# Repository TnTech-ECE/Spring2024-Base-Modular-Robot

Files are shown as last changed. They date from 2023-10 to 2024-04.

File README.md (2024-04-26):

# Modular IEEE Robot

## Executive Summary

Each year, Tennessee Technological University (Tech) participates in the Institute of Electrical and Electronics Engineers (IEEE) Southeastern Conference (SECON) hardware competition. The competition asks participants to create a robot that can perform various tasks, and competitors are scored based on their robot’s capability to complete tasks as quickly as possible. In past years, Tech has placed well, but the same problems have arisen each year that have inhibited wins: choppy navigation, shorted cables, and battery depletion are just a few of the many problems teams have repeatedly faced in previous competitions. The team sets out to fix the besetting problems that teams face each year not by competing in SECON, but rather by building a generalized platform that will optimize the basic robotic functionality for future teams. Sensing, movement, and centralized charging are the top priorities in the team’s design, all fitted together in a modular, adaptable framework that can be manipulated to fit most – if not all – IEEE hardware competition specifications. No longer will teams have to spend countless hours learning and designing movement systems or hoping everything works after rewiring a battery mid-competition. The design will take care of these basic competition necessities and leave the custom tailoring to the competition team.  

## Capabilities

The current version of the robot has the following capabilities:
1. Autonomous navigation
2. Modular components that can be easily adapted for different uses
3. Robust, centralized charging system
4. Functioning emergency stop button
5. Can travel inclines and declines up to 25 degrees
7. 360 degrees of movement
8. Knows location within a 2 inch tolerance
9. Sensors are are plug and play adpatable with the use of an I2C bus
10. Foundation layed for autonomous navgivaton with LiDAR and ROS2
11. User manual for teams to understand design considerations, common problems, and solutions

## Salient Outcomes

As projects progress, there are typically outcomes tht are more impressive than others. Here is a list of salient outcomes of this project:
1. Wireless charging proof of concept
2. Multiple navigation subsets for teams to choose between
3. Foundation for layed for ROS2 mapping for future uses
4. Plug and play adapatibility with sensors through I2C buses
5. Power board with ground isolation
6. GUI for teams to see their live data transmission 

## Project Demonstration & Images

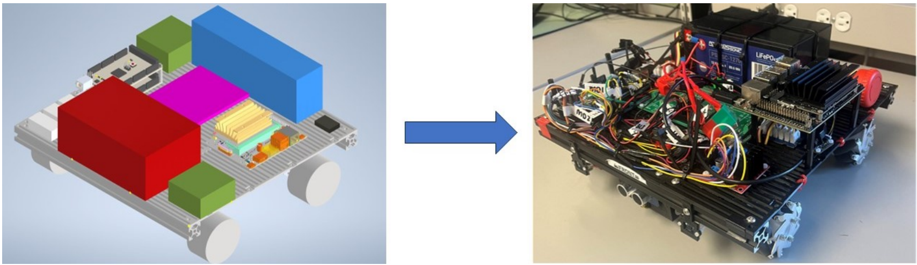
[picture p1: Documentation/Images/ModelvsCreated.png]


3D model of the robot vs the final product

[Watch the video](https://youtu.be/stM9KGa8I_E) of the robot autonomously navigating a line.

[Watch the video](https://youtu.be/3MeIy1WahUA) of the robot autonomously sweeping the board given its location.

[Watch the video](https://youtu.be/3MeIy1WahUA](https://www.youtube.com/watch?v=_iFhnvbLboQ)) of the robot detecting objects in front of it.

## About Us

### Team

**[Luke Chapman](https://www.linkedin.com/in/luke-chapman-/)** is an electrical engineering major at Tennessee Technological University with a minor in mathematics. He is interested in electromagnetics, telecommunications, and signal processing. Luke is responsible for the power management and distribution systems of the robot as well as the experimental wireless power charging system.

**[Reid Crews](https://www.linkedin.com/in/jackson-crews-381187257/)** is an electrical engineering major, mechatronics concentration at Tennessee Technological University with a minor in mathematics. Reid's interests are mechatronics and control systems. For the project, Reid is a contributor for the navigation sensing, primarily the location and object detection subsystems.

**[Isaac Hoese](https://www.linkedin.com/in/isaac-hoese-425748251)** is a senior electrical engineering student from Greeneville, Tn. He is interested in both power system analysis and embedded system design. In this project, Isaac will be a contributor for the navigation sensing, primarily the line following and orientation subsystems.

**[Isaac Jennings](www.linkedin.com/in/isaac-jennings-a04680209)** is a senior electrical engineering student with a minor in mathematics from Church Hill, TN. He takes interest in control systems, programming, and embedded systems, which is where he allocated his time by working on the master control systems on the project. He is responsible for the navigation and localization of the robot as it interfaces with the game board.  

**[Abigail Kennedy](https://www.linkedin.com/in/abigail-kennedy-tech/)** is an electrical engineering major at Tennessee Technological University with minors in mathematics and education. Abigail's primary interest is in controls and PLC design, and for this project, she worked on the motor control subsystem to ensure the robot can move quickly and smoothly.

**[Mabel Olson](https://www.linkedin.com/in/mabelolson/)** is an electrical engineering major at Tennessee Technological University with a minor in mathematics. She is intrested in power and control systems. In this project, Mabel is responsible for the chassis design, robot layout, organization, and any 3D designing of component attachment pieces. 

### Faculty Supervisor

The faculty supervisor for this project is [Dr. Nan Chen][def1]. She completed her electrical and control engineering Bachelor's degree from Nanjing University of Aeronautics and Astronautics. She also completed her Master's and Ph.D. in electrical engineering from the University of Waterloo. 

[def1]: https://www.linkedin.com/in/nan-chen-319aa185/

### Stakeholders

The primary customer for the project is [Professor Jesse Roberts](https://www.linkedin.com/in/jessetnroberts/) - the advisor for the IEEE SECON hardware teams. Future teams are impacted by this design but unable to be stakeholders, so he gives input on their behalf based on his years of experience with the competition.

### Recognitions

We would like to recognize and thank Professor Jesse Roberts, Dr. Nan Chen, and Dr. Charles Van Neste for their continuous input and guidance on the project.

## Repo Organization

### [Reports](/Reports)

The [Project Proposal](./Reports/Project%20Proposal/Project%20Proposal%20Revised.pdf) is the initial document for the project where the problem is defined and the goals for the project.

The [Conceptual Design](./Reports/Conceptual%20Design/Conceptual%20Design%20and%20Planning%20V2.pdf) gives a more detailed solution to the problem as well as subsystem breakdowns and a projected timeline and budget.

The [Experimentation](/Documentation/Experimental%20Analysis) gives the experimental results of the different subsystems and how constraints were met or not.

The [Poster](./Reports/Poster/Modular%20IEEE%20Robot%20Poster.pdf) is what the team presented at the 2024 capstone showcase.

The [Final Presentation](./Reports/Final%20Presentation/Final%20Presentation.pdf) is the presentation that the team gave to the IAB.

The [Lessons Learned](./Reports/LessonsLearnedAndAquiredSkills.md) gives team members' reflections on their progress, oversights, noteable incidents, and successes.

### [Documentation](/Documentation)
All documentation for the project is included in the above folder. Documentation includes all schematics, images, models, BOM, and designs used in the project.

The [Meeting Minutes](/Documentation/Meeting%20Minutes) folder contains the dated minutes from weekly meetings and allows a quick view into the progress of the team.

[Signoffs](/Documentation/Signoffs) are used to finalize designs for each subsystem. This includes schematics, design decisions, BOM, and analysis. 

### [Software](/Software)

 All software used and created is listed in the [Software](./Software) directory. For each subsystem, there are specific folders listed to find the necessary code.

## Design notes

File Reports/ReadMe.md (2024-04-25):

# Reports

The final version of the following are found here in Reports:

1. [Project Proposal](https://github.com/lchapman42/Control-Sensing-Wireless-Charging-Robot/blob/main/Reports/Project%20Proposal/Project%20Proposal%20Revised.pdf)
2. [Conceptual Design and Planning](https://github.com/lchapman42/Control-Sensing-Wireless-Charging-Robot/blob/main/Reports/Conceptual%20Design/Conceptual%20Design%20and%20Planning%20V2.pdf)
3. [Poster](https://github.com/lchapman42/Control-Sensing-Wireless-Charging-Robot/blob/main/Reports/Poster/Modular%20IEEE%20Robot%20Poster.pdf)
4. [Lessons Learned](https://github.com/lchapman42/Control-Sensing-Wireless-Charging-Robot/blob/main/Reports/LessonsLearnedAndAquiredSkills.md)
5. [Final Presentation](https://github.com/lchapman42/Control-Sensing-Wireless-Charging-Robot/blob/main/Reports/Final%20Presentation/Final%20Presentation.pdf)

## Examples

The following capstone projects were helpful in writing our reports:

[SECON 2022](https://github.com/TnTech-ECE/Spring2022-SECON2022)

[SECON 2023](https://github.com/TnTech-ECE/Spring2023-SECONRobot)

[Crawlspace Robot](https://github.com/TnTech-ECE/Fall-2023-2.0-Autonomous-Crawlspace-Inspection-Robot)

[Active Noise Control](https://github.com/CarsonDPope/Active-Noise-Control-With-Wall-Transmission-Detection)

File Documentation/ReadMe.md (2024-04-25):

# Documentation

Each of the folders have the team's designs, research, and useful images used for the project. It also contains the team's meeting notes and plans for the future of the project. A final BOM was determined after purchasing everything for this iteration.

## Signoffs

Signoffs are the detailed part of the design process which includes the schematics, bill of materials, specifications, and justifications. The signoffs have been approved by Dr. Nan Chen and were also advised by Dr. Jessee Roberts.

## Final set of prints (final design artifacts)



### 3D Models

Required format: 
3D models can be found [here](https://github.com/lchapman42/Control-Sensing-Wireless-Charging-Robot/tree/main/Documentation/3D%20Models), and they have been updated throughout the project.

### Wiring Schematics and PCB

All schematics and PCB designs can be found [here](https://github.com/lchapman42/Control-Sensing-Wireless-Charging-Robot/tree/main/Documentation/Electrical). 

## Final BOM

The final version of the BOM can be seen as a [pdf](https://github.com/lchapman42/Control-Sensing-Wireless-Charging-Robot/blob/main/Documentation/Final%20BOM.pdf) or in the original [exel file](https://github.com/lchapman42/Control-Sensing-Wireless-Charging-Robot/blob/main/Documentation/Final%20BOM.xlsx).

## Datasheet 

The [user manual](https://github.com/lchapman42/Control-Sensing-Wireless-Charging-Robot/tree/main/Reports) in the reports section can be used to see how each of the subsystems work in detail and connect.

## The project poster

The project poster that summarizes the final results of the project is [here](https://github.com/lchapman42/Control-Sensing-Wireless-Charging-Robot/tree/main/Reports/Poster).

## Detailed photos of the project

Detailed photos of the project can be found [here](https://github.com/lchapman42/Control-Sensing-Wireless-Charging-Robot/tree/main/Documentation/Images).

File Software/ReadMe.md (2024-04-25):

## Bluetooth Reveiver
This code is for an ESP32. The reciever microcontroller needs to be connected to a laptop. The GUI can be ran to read sensor data when the Nav_Full code is ran. The code recieves the signal sent by the transmitter.

## Bluetooth Transmitter
This code is for an ESP32. The transmitter micrconcontroller needs to be connected to the on-robot Arduino Mega 2560. The code creates ESP Now packets to be sent to the reciever.

## 2023_Board
This code is ran on the on-robot Arduino Mega 2560 for object detection and position sensing without a line present. (Not used with ROS)

## Line Following
This code is ran on the on-robot Arduino Mega 2560 for line following. The code uses PID control method to control navigation. (Not used with ROS)

## Nav_Full 
This code is ran on the on-robot Arduino Mega 2560. This code encapsulates all sensor readings and is used alongside the jetson nano. The code has no navigation capability as ROS completes those tasks.

*All Arduino Mega and ESP32 code is compiled with the Arduino IDE*

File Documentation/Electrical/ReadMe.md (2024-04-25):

This directory contains all of the electrical schematics and PCB files. The PCB directory contains files for the simulation, schematics, and design of the power distribution PCB. The Schematics directory contains the files for the Arduino schematic. The Testing directory contains data from testing the battery life and some notes taken while performing tests on the different power subsystems.

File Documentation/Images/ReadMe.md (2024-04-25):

This directory contains images used in each of the signoffs and experimental analysis, they are elaborated in their respective sections:
- [Signoffs](https://github.com/lchapman42/Control-Sensing-Wireless-Charging-Robot/tree/main/Documentation/Signoffs)
- [Experimental Anaylsis](https://github.com/lchapman42/Control-Sensing-Wireless-Charging-Robot/blob/main/Documentation/Experimental%20Analysis/Experimental%20Analysis.md)

There are also videos of different experiments and the robot movement in the experimental analysis section.

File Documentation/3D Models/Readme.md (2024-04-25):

The 3D models directory has the .stl files for the 3D printed components created for this project.

The .stl files can be viewed in GitHub and used with other 3D editing software. Please see the respective sign offs for more information on the components.

- [Attachments](https://github.com/lchapman42/Control-Sensing-Wireless-Charging-Robot/blob/main/Documentation/Signoffs/Attachment%20Signoff.md)
- [Chassis](https://github.com/lchapman42/Control-Sensing-Wireless-Charging-Robot/blob/main/Documentation/Signoffs/Chassis%20Frame%20Sign%20Off.md)
- [Layout & Organization](https://github.com/lchapman42/Control-Sensing-Wireless-Charging-Robot/blob/main/Documentation/Signoffs/Layout%20and%20Organization.md)

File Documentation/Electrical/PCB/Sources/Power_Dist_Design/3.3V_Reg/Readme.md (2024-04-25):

In this directory there are files for a SPICE simulation of the buck converter chip. The SPICE model of the buck converter was gotten from the manufacturer, Texas Instruments. To perform the simulation simply run the .asc file with LTSpice or another SPICE simulation software. There is only a simulation of the 3.3V layout, there was 5V layout originally but it was removed on accident some time ago. The only difference between the 3.3V and 5V simulations is a single resistor value, which can be easily determined in the datasheet. This is discussed more in the signoff for the power distribution system.

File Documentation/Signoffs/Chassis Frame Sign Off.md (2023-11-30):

# Chassis Frame Signoff

## Functionality 

The function of this subsystem is to be the structure of the robot. This will allow ll components to be connected together through a strong frame.

## Constraints

- C3: The robot shall be autonomous with customizable dimensions and the stock design only occupying up to one-half of the allowed cubic foot (1 ft x 1 ft x 6 in).
	- This constraint is applicable to the chassis frame because the frame will be the standward way for custom dimensions. Therefore, the material needs to allow for easy movement of sides, come in multiple sizes, and be able to be cut if possible. It is important to note that the stock design will be occupying 1 foot by 1 foot area. The height will be mainly effected by the motors, components, and their trays.

- C4: The robot shall contain modules that are plug and play adaptable for different IEEE competition requirements.
	- This constraint is applicable to the chassis frame subsystem because components need to have the ability to be added, removed, and or moved easily. The chassis frame will be what every component is attached to; therefore, the a material selected needs to allow for easy attachment method.

### Derived from Broader Impacts

- The frame will need to be able to withstand 20 pounds.
	- This stems from a typical weight standard of 25 pounds that had to be reduced due by the customer due to not being able to reach an incline and speed specifcation with a 25 pound load with avaliable motors.

## Buildable Schematics
The following schematics outline the dimensions for the extrusion itself and the layout for the chassis. The chassis frame layout was decided through many decisions. Trying to take up as much of the 1 foot by 1 foot area was the largest concern. 1 foot is 304.8 mm. Therefore, the 300 mm frame peices were used for the front and rear bars. The 250 mm bars are used for the side bars and nested inside the 300 mm bars. This will make the width to be 300 mm and the length to be 290 mm because the width of the bars is 20 mm. The side bars are nested inside due to the motors and wheels. They add width to the frame and therefore if the bars are nested they can be moved in or out to adhere to dimension requirements. The placement in the schematics allow for maximum occupency of the space. The middle bar is there to add more support and for better tray movement, but can be removed if decided that it is not needed in the tray subsystem. The middle rod does not have to be centralized as it is in the schematic. It can be moved based on what is needed for the tray sizes.  
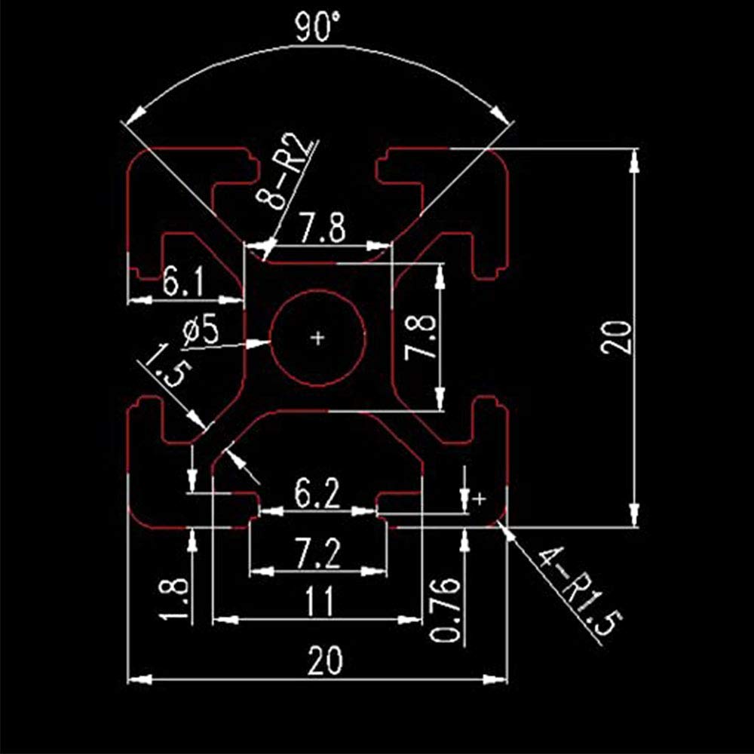
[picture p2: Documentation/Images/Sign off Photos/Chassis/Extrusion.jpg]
  
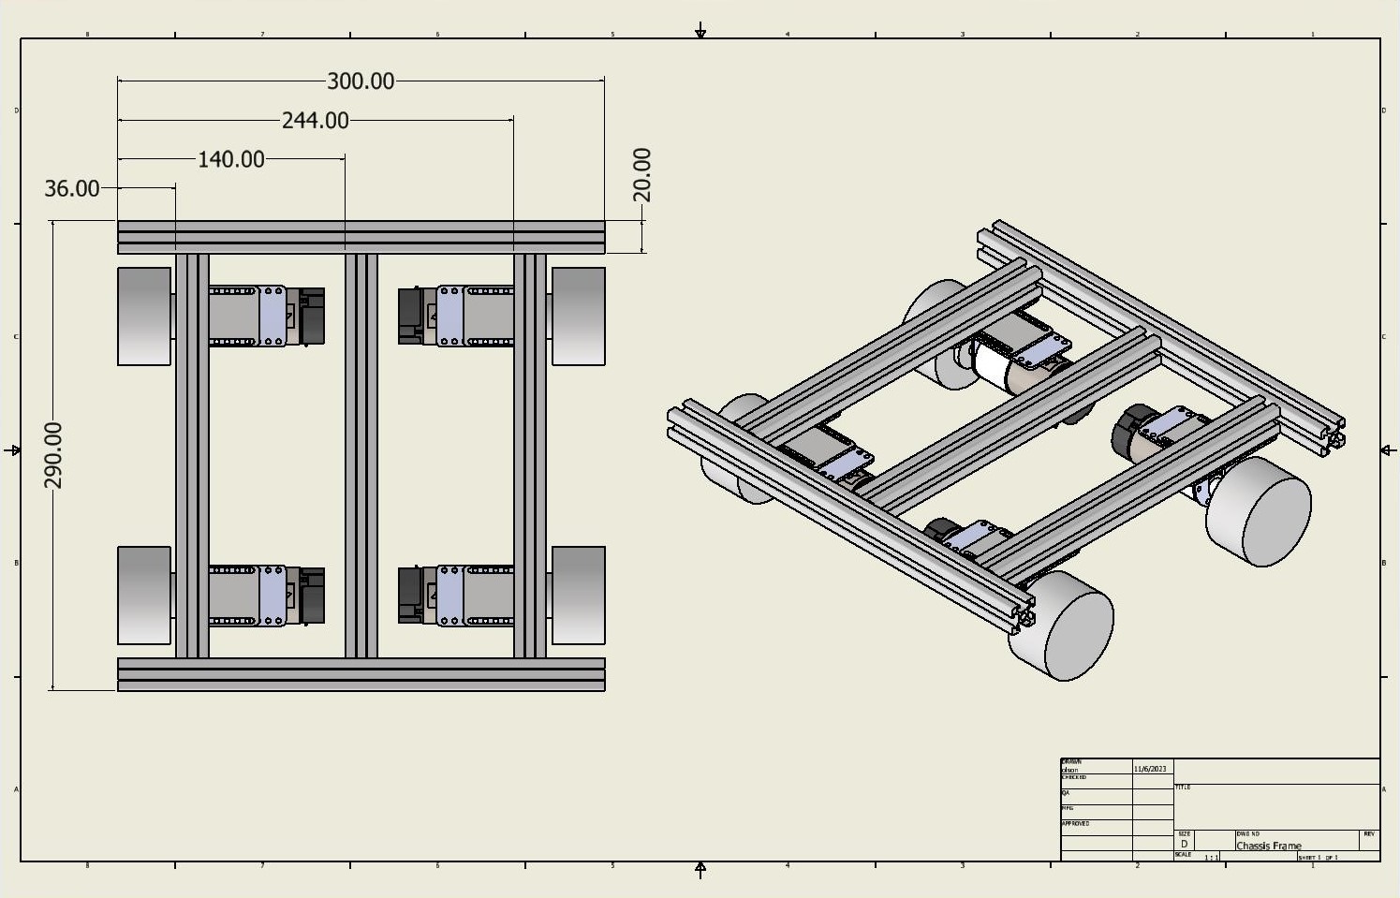
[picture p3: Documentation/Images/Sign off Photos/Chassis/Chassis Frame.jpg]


## Analysis
The following analysis section will calculate if the extruded alumninum can withstand the maximum 20 pound load it aims to withstand.  
  
$\sigma_{b} = \frac{ My }{I}$  
  
$\sigma_{b} = \sigma_{Yield Strength} = 16$ ksi (kilopound per square inch)
     
This value comes from the material itself: 6063 Aluminum - T5 Alloy.  
  
M = $\frac{P_{max}L}{4}$  
  
L = 250 mm = 9.842520 in  
   
These two values are important because we are after $\ P_{max}. P_{max}$ is the maximum allowable pressure that the component can withstand before any sort of deflection in the material occurs. L is the length of the shortest component used.   
  
y = 10 mm = 0.393701 in  
   
I = $\ 0.6826 cm^4 = 0.0163995 in^4$  
    
y is the distance from center of the extrusion to the outside edge. I is the moment of interia. This is a constant based on the shape of the component. This specific manufacturer did not provide the moment of interia; however, a manufacturer with a nearly identical component was found and used for calculation. Once the value is calculated, it was discovered that any difference would be negliable due to the magnitude of the pressure compared to the weight we are aiming to hold as well as the fact that the weight will be distributed. This calculation is how much pressure it would take to deflect if that full weight was placed on a single point of the component. Additionally, this is just considering a single 250 mm long bar. In reality the weight will be distributed roughly evenly across all bars.
  
Therefore, with all this the following $\ P_{max}$ can be calculated.  
   
=> 16 ksi = $\frac{ \frac{P_{max}L}{4}(0.393701 in)}{0.0163995 in^4}$   
   
=> $\ P_{max}L$ = 2.6659 kip-in  
   
=> $\ P_{max} = \frac{2.6659 kip-in}{9.842520 in}$ = 0.270855 kip = 270.855 lbf (pound force)   
  
This means that it would take 270.855 pounds of force on a single point of the extuded aluminum for deflection to occur. This is more than 13 times the amount the team is aiming to hold. Therefore, the frame can easily withstand the weight requirement.  

## BOM
| Item | Quantity | Price/Item | Total Price | 
|-|-|-|-|
| 250 mm Extruded Alumnium (4 pk)| 1 | $16.99 | $16.99 |
| 300 mm Extruded Alumnium (4 pk)| 1 | $17.99 | $17.99 |
| 6 mm Alumnium Corner Connectors (20 pk)| 1 | $13.64 | $13.64 |
| | | | $48.62 |

## References
Extrusion : https://www.amazon.com/Aluminum-Extrusion-European-Standard-Anodized/dp/B08CN92SP1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  
Moment of Inertia : https://8020.net/20-2020.html  
Extruded Aluminum Data : https://web.archive.org/web/20031006212043/http:/www.alcoa.com/adip/catalog/pdf/Extruded_Alloy_6063.pdf  
Strength Equations : R. C. Hibbeler, Mechanics of Materials, 10th Ed. Hoboken, NJ, USA: Pearson, 2015.

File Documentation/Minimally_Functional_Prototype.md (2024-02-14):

**Minimally Functional Prototype Checklist as of 2/8/24**

- [ ] Start button/switch 
- [ ] Be able to move the motors 
- [ ] Easily connectable power buses for voltages 
- [ ] Sensor connections easily changeable 
- [ ] Proper voltages from power buses 
- [ ] Emergency Stop button 
- [ ] ESP bluetooth communcation to show sensor data

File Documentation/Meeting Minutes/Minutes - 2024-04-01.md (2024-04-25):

# Group 7 Meeting Minutes 24-04-01

## Attendance:

**In-Person:**\
Abigail Kennedy\
Reid Crews\
Isaac Hoese\
Mabel Olson\
Luke Chapman\
Isaac Jennings

**Remote:**

## Team Member Updates

Mabel:\
Created an experimental analysis (EA) markdown file for everyone to add their sections to the signoffs. Almost done with experimental analysis and manual.

Isaac J:\
Got serial communication working. The issue was from the baudrate variables being defined within a class. Will meet up with Isaac H to get sensor communication finalized.

Abigail:\
Manual almost done. Doing EA stuff today. Will work on navigation stuff with Isaac J this week.

Luke:\
Replaced the diodes with capacitors on the power boards. First board's 3.3 V bus began having issues, sometimes outputting the incorrect voltage, unsure if related to driver failure. Replaced with backup board which works fine. Motors and motor drivers work fine. Hypothesis that driver failure was heat-related from the constant switching of the motors. 

Isaac H:\
Worked on user manual, will continue working on it this week. All subsystems should be pretty much done. Will help Isaac J with navigation this week.

Reid:\
Started on EA, need to finish. Worked on user manual. Sensor precision has been under an inch so far, much better than the required 2 inch precision.

## Action Items from Last Meeting

## Meeting Minutes

Make sure all constraints are discussed in experimental analysis, not just the ones derived from shall statements.

Should mention in the manual to get all components placed before moving things around.

Will take team photo during meeting time next Monday (4/8/24). Business casual is the dress code for the picture.

## Action Items for Next Meeting

Go over progress on EA.

## Member Assignments

Continue working on EA.

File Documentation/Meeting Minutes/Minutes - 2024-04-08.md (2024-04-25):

# Group 7 Meeting Minutes 24-04-08

## Attendance:

**In-Person:**\
Abigail Kennedy\
Isaac Hoese\
Isaac Jennings\
Mabel Olson\
Reid Crews\
Luke Chapman

**Remote:**\

## Team Member Updates

Progress made on nav and sensor communication. Robot seems to have difficulty getting over the hills while line sensing since the motors aren't run at maximum power while the line-sensing correction program is running.

Added line to the flat arena to test the line following more. Will test the line following and incline traversing separately.

## Action Items from Last Meeting

Go over progress on EA.

## Meeting Minutes

Talked to Roberts about using Lidar for the mapping. Could just show that the robot can map the hallway. Rev2 can have the battery sit lower in the robot and have the lidar.

Instead of waiting for the battery to completely die, can use curve matching using the datasheet to estiate from data.

Robot can navigate the flat arena almost entirely. 

Took pictures for the capstone poster.

Discussed the robot doing a sweep of the flat arena.

## Action Items for Next Meeting

## Member Assignments

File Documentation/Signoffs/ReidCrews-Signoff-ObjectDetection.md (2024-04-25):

# Object Detection Signoff

## Functionality

The object detection subsystem sends data to the master control  to control and move the robot. The subsystem will use time of flight distance sensors to detect object inside of the arena. The time of flight sensors will use the detected object to determine the robot's movement to avoid the object. The emitter will use a laser shot infrared light, and the collector will recieve the reflected light that bounces off objects. This data will be sent to the master control to move and control the robot to avoid the object(s).

## Constraints
### Shall Statements

* C4: The robot shall contain modules that are plug-and-play adaptable for different IEEE competition requirements. 

    * This constraint allows future teams to replace or reallocate the chosen object detection sensor(s).

* C10: The robot shall turn 360 degrees left and right and move forwards and backwards based on sensor inputs.
    
    * This constraint is applicable because the robot needs to move around the arena autonomously.

* C11: The robot shall have a navigation system that controls movement.

    * This constraint is applicable because the sensor needs to transmit data to the master control.

### Broader Implications

* C14: The robot shall have a user manual that explains all functions and capabilities of the robot. 
	
    * This constraint was constructed to document the design process and motives of the object detection subsystem for future SECON teams.
    
## Buildable schematic 

### Object Detection Subsystem Schematic

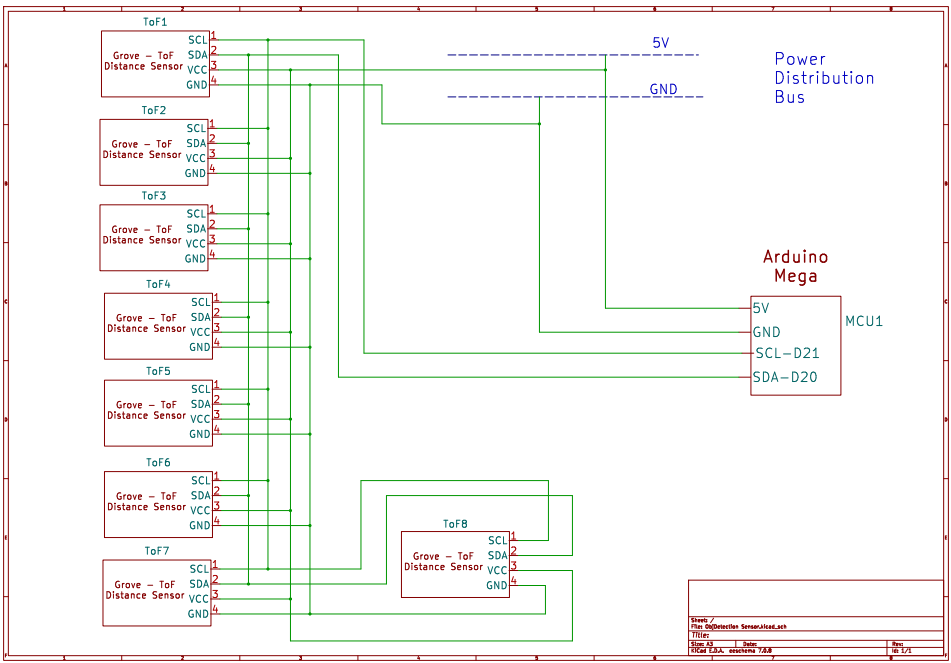
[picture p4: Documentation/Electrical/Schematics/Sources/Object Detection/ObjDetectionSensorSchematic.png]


The schematic above is shown. Eight time of flight are used for the object detection with two sensors per each side. Each sensor is I2C communications. Each sensor has a serial clock (SCL) connected to digtial pin 21 of the Arduino Mega. Each sensor also has a serial data (SDA) connected to digtial pin 20 of the Arduino Mega. Each sensor and Arduino Mega are powerd by the 5 V power distribution bus.
<br/>
<br/>
<br/>

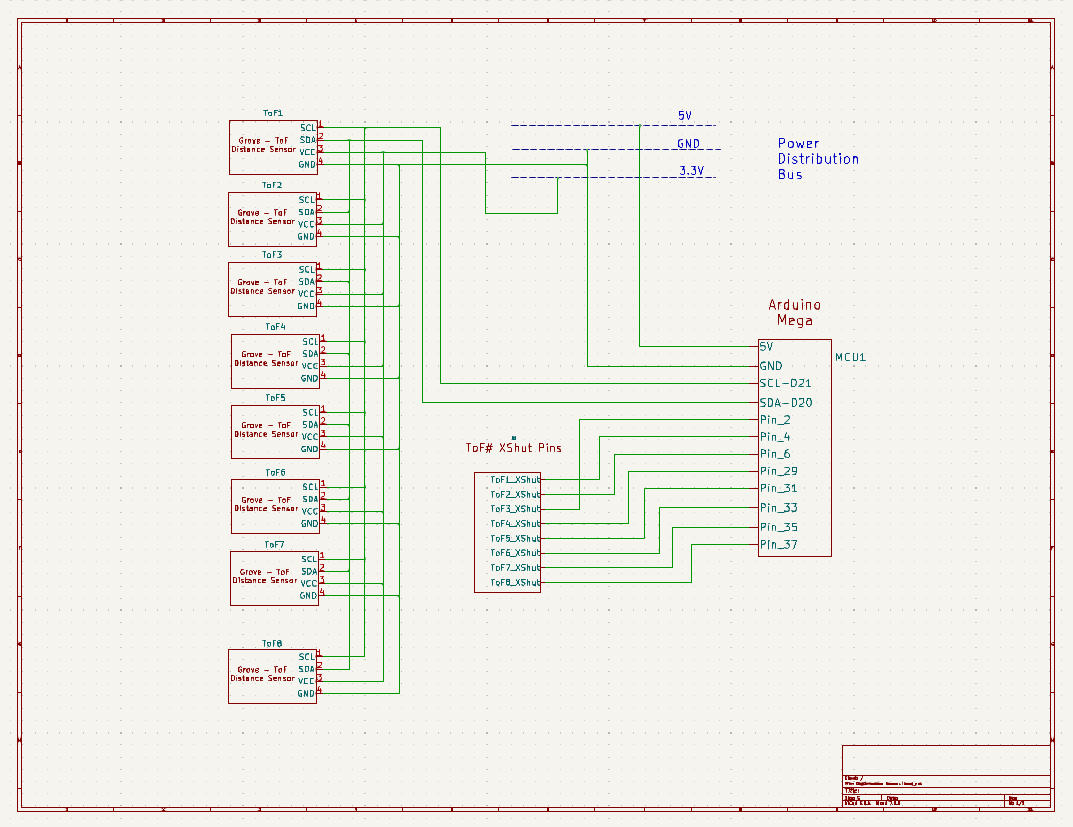
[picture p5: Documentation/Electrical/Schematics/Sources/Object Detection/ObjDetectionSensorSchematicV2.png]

<br/>
**The schematic above is the revised schematic with the 8 ToF XSHUT Pins to intialize each sensor with a new address**

### Object Detection Placement

<p align = "center">

</p>

The CAD drawing above is the horizontal view of the time of flight. The field of view (FOV) is 25 $^\circ$. The maxmium recommended distance is 1 m (39.37 in). 

<p align = "center">

</p>

The CAD drawing above is the vertical view of the time of flight.

## Analysis

The time of flight sensor has an operating current at 19 mA and operating voltage at 5 V. The Grove Time of Flight Disyance Sensor requires only two pin for SCL and SDA. The picture below shows the plug-and-play ability because the sensor can be connected the GROVE connectors.

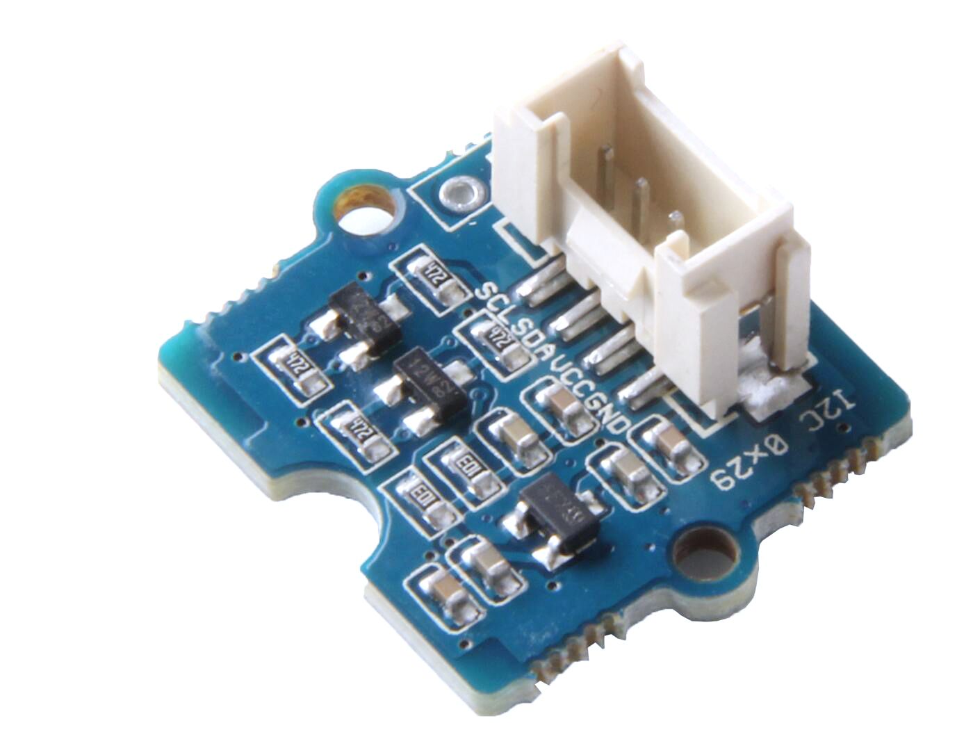
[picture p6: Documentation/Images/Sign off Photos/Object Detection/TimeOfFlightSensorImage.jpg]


From the CAD drawing of the horizontal view of the timing of flight, the equation for the blind spot (the area in the middle of the two sensor's FOV).

$$ Max \space Distance = {x \over 2} * tan(77.5^\circ)$$

The *Max Distance* is max distance in the blind spot and *x* is the distance between the two sensors. For the CAD drawing case, the *Max Distance* is 13.53 in, and the area is 40.59 in $^2$. For the maxmium apart case (12 in apart), *Max Distance* is 54.12 in, and the area is 324.77 in $^2$. The chosen distance between the sensors is 6 in becuase the max distance from edges and blind spot is the lowest average distance. The blue and green lines are 13.53 in.

<p align = "center">

</p>

The sampling rate for the time of flight sensor 33 ms at default. The minimum is 8 ms, and the maximum is 200 ms. The default frequency is 30.3 Hz. The time of flight sensor has four modes in the table below [1-2].

<p align = "center">
Table 1: Four Modes

<div align="center">
	
| Range profile | Range timing budget | Typical performance | Typical application |
|---|---|---|---|
| Default mode  | 30 ms | 1.2 m, accuracy 4 % - 7 % | Standard |
| High accuracy | 200 ms | 1.2 m, accuracy < +/- 3 % | Precise measurement | 
| Long range | 33 ms | 2 m, accuracy 4 % - 7 % | Long ranging |
| High speed | 20 ms | 1.2 m, accuracy +/- 5 % | High speed |
	
</div>
 
These modes allow the team to prioritize either accuracy, range, or speed. Range timing budget is the sampling rate. 

$$ Max \space robot \space speed: \space 2 \space {ft \over s}$$

$$ \space $$

$$ Sampling \space Rate \space for \space Default \space Mode \space 30\space ms\space (33.3\space Hz)$$

$$ 2 \space {ft \over s} *0.03 \space s = 0.06 \space ft \space or \space 0.72 \space in $$

$$ Accuracy \space Range \space for \space Default \space Mode $$

$$ 4 \space Percent \space (0.6912 - 0.7488 \space in) \space , \space 7 \space Percent \space (0.6696 - 0.7704 \space in) $$

$$ \space $$

$$ Sampling \space Rate \space for \space High \space Speed \space Mode \space 20\space ms\space (50\space Hz)$$

$$ 2 \space {ft \over s} *0.02 \space s = 0.04 \space ft \space or \space 0.48 \space in $$

$$ Accuracy \space Range \space for \space High \space Speed \space Mode $$

$$ 5 \space Percent \space (0.456 - 0.504 \space in) \space $$

Default Mode is the chosen mode because the sampling rate is the second highest and accuracy range is tied for second lowest. The Default Mode has the best specifications out of the four modes. <br />
<br />

See [Seeed Studio Forum](https://forum.seeedstudio.com/t/how-to-change-i2c-address-on-grove-time-of-flight-distance-sensor-vl53l0x/266866/2) on how to use multiple VL53L0X time of flight sensors.

## BOM

<div align="center">

| Item | Part Number | Quantity | Price | Total Price | 
|-|-|-|-|-|
|Grove - Time of Flight Distance Sensor(VL53L0X) | SKU 101020532 | 8 | $36.99 | $295.92| 

</div>

## Reference

[1] [User Manual Time of Flight][def1]: User Manual for VL53L0X

[2] [Datasheet Time of Flight][def2]: Datasheet for VL53L0X

[3] [Seeed Studio Website][def3]: Time of Flight Sensor Website

[4] [Purchase Site for Sensor][def4]: Amazon Site of Time of Flight Sensor

[def1]: https://github.com/lchapman42/Control-Sensing-Wireless-Charging-Robot/blob/main/Documentation/Background%20Documents/Object%20Detection/Time-of-Flight%20User%20Manua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

[def2]: https://github.com/lchapman42/Control-Sensing-Wireless-Charging-Robot/blob/main/Documentation/Background%20Documents/Object%20Detection/Time-of-Flight%20Datasheet.pd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

[def3]: https://www.seeedstudio.com/Grove-Time-of-Flight-Distance-Sensor-VL53L0X.html?utm_source=blog&utm_medium=blog

[def4]: https://www.amazon.com/SeeedStudio-Grove-Flight-Distance-VL53L0X/dp/B07Q1YBH99?ref_=ast_sto_dp

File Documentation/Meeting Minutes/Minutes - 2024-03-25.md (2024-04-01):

# Group 7 Meeting Minutes 24-03-25

## Attendance:

**In-Person:**\
Abigail Kennedy\
Reid Crews\
Isaac Hoese\
Isaac Jennings\
Luke Chapman\
Mabel Olson\

**Remote:**\

## Team Member Updates

Team members continued working on subsystems for experimental analysis (EA).

Isaac H:\
One of the line sensors stopped working, started sending all zeros. Something may have gotten shorted when thing were being moved. Otherwise, sensor readout is working and have some communication between sensors, arduinos, and jetson nano. Figured out why I2C sensors werent working - They were sending 3.3 V signals, but receiving 5 V signals. Moving everything over to 3.3 V rails fixed it.

Mabel:\
Updated sensor attachments and sent to makerspace. Worked on user manual.

Luke:\
Worked on manual, tested the twisted pair cable which seems to not work. Got a basic CPT setup working, need to ask Roberts how far need need to go with the CPT setup. Finished manual as well.

Abigail:\
Worked more on motor code for communication and got steering working. Will work more on motor code.

Isaac J:\
Worked on getting comms working, motor comm almost works. Sensor communication working.

Reid:\
Picked out locations for measurements for EA, 

## Action Items from Last Meeting

Go over measures of success.

## Meeting Minutes

Will add a button to the jetson nano to have a start button that doesn't connect all power to the robot.

Talk to Roberts about:
- Wireless charging on experimental analysis
- If 22.5 degree incline/decline is acceptable
- User manual and getting feedback

## Action Items for Next Meeting

Talk to Dr Chen about what she expects from the EA.

## Member Assignments

Continue working on respective parts for the EA.

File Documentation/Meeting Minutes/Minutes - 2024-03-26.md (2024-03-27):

# Group 7 Advisor Meeting Minutes 24-03-26

## Attendance:

**In-Person:**\
Abigail Kennedy\
Reid Crews\
Isaac Hoese\
Mabel Olson\
Luke Chapman\
Nan Chen

**Remote:**\
Isaac Jennings

## Team Member Updates

Team members continued working on experimental analysis (EA).

## Action Items from Last Meeting

Discuss with Dr. Chen about expectations for the EA.

## Meeting Minutes

Dr Chen said it is acceptable to only test using the existing 22.5 degree incline.

Dr. Chen wants robot to ideally be able to maneuver around obstacles. Don't need to do 2 boards, but if can demo obstacle maneuvering and line following on one board, that is acceptable. Location within 2 inch tolerance too.

For user manual, it is acceptable to just show Dr. Chen what we have with the user manual for the EA deadline.

For capacitive power transfer, it is acceptable to provide plans/ideas for future teams to expand on the system from where the system is now.

Discussed doing meeting next Thursday instead of Tuesday. 

## Action Items for Next Meeting

Go over progress on EA. Discuss with Roberts about EA expectations.

## Member Assignments

Continue working on EA.

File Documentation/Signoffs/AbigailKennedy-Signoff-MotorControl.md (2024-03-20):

# Motor Control Subsystem
## Function of the Subsystem
The motor control subsystem takes serial signals from the master control and determines the signals to send to the motor drivers to move the robot. To be successful, the robot must be able to move with a maximum speed of 2 ft/s, move up an incline of 25 degrees, turn 360 degrees, and move forward and backward. 

## Constraints
- C9: The robot shall travel inclines and declines up to 25 degrees. 
- C10: The robot shall turn 360 degrees left and right and move forwards and backward based on sensor inputs.
- C13: The robot shall possess a maximum speed of 2 feet per second.
- The robot's speed will be calculated assuming the robot weighs 20 pounds. This is done due to the maximum weight limit for competition.

### Socioeconomic Consideration
- The motors chosen should operate at about 70% of the maximum efficiency to ensure power can be conserved and to reduce charging costs. Additionally, this will give the robot enough extra power when traversing inclines. 
- C14: The robot shall have a user manual that explains all functions and capabilities of the robot. 
        - The work done on this design and the implementation will be documented thoroughly to ensure the user manual is as helpful as possible for future groups using the robot.

## Buildable Schematics

### Electrical Schematic
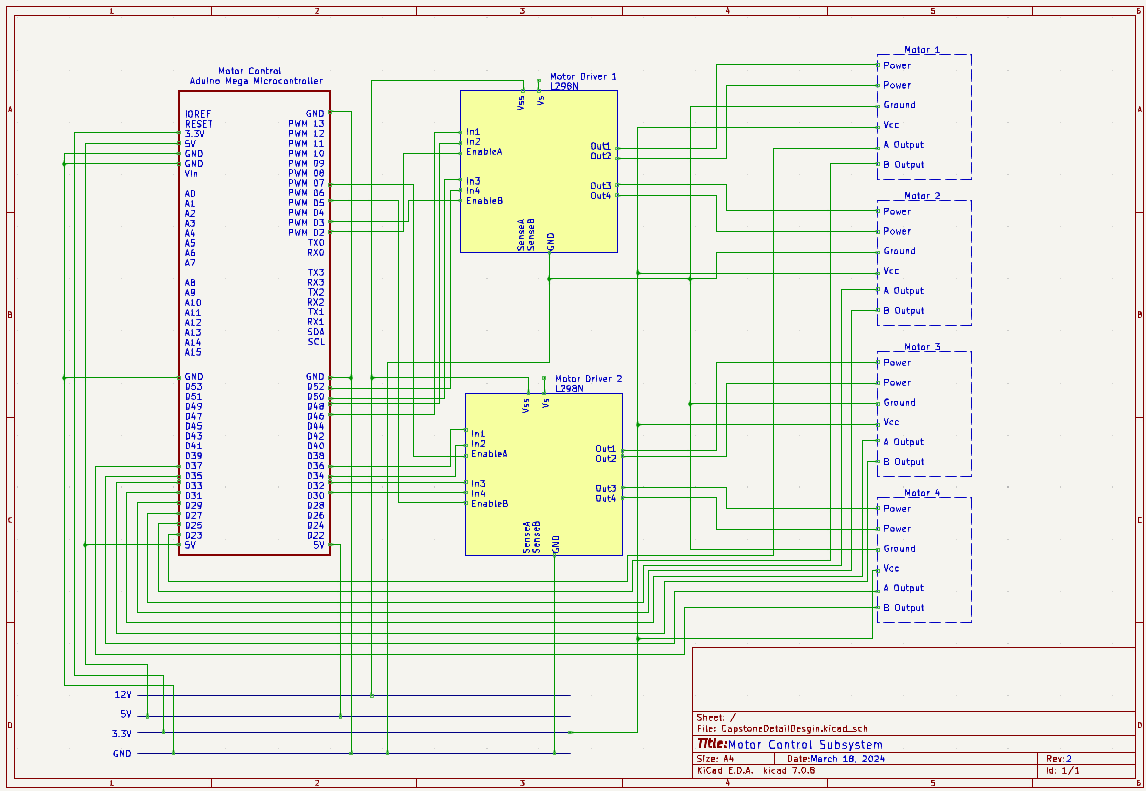
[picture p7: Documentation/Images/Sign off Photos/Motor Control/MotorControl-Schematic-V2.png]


This electrical schematic shows the connections between the microcontroller [1], motor drivers [2], and motors [3]. This microcontroller - Arduino Mega - was chosen due to the number of analog ports available since those are needed to communicate with the motor drivers. This is the same microcontroller used by past SECON robot teams for motor control, so that it will have the capabilities required for the communication from master control to the motor drivers. The motors chosen are similar to ones from past years, but these are larger and have more torque to meet the new obstacle of moving up an incline and the possibility of the robot being double the weight of past robots. The maximum torque needed was calculated to prepare for the worst-case scenario (found in the analysis subsection). When the motors run, they should pull 0.72 A, well below the 2 A maximum rating output current for each driver channel. This driver was chosen since past teams successfully used it, and it can power the motors successfully. All the selected components are connected to either 3.3 V, 5 V, or 12 V based on their specific power ratings in the datasheets. 

### Motor and Wheel Assembly
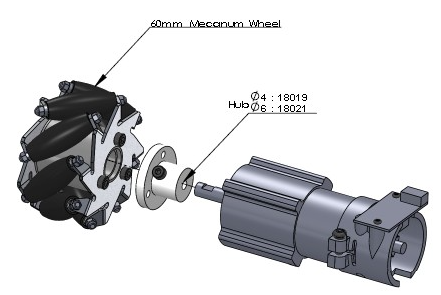
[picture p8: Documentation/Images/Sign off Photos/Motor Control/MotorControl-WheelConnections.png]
inamge


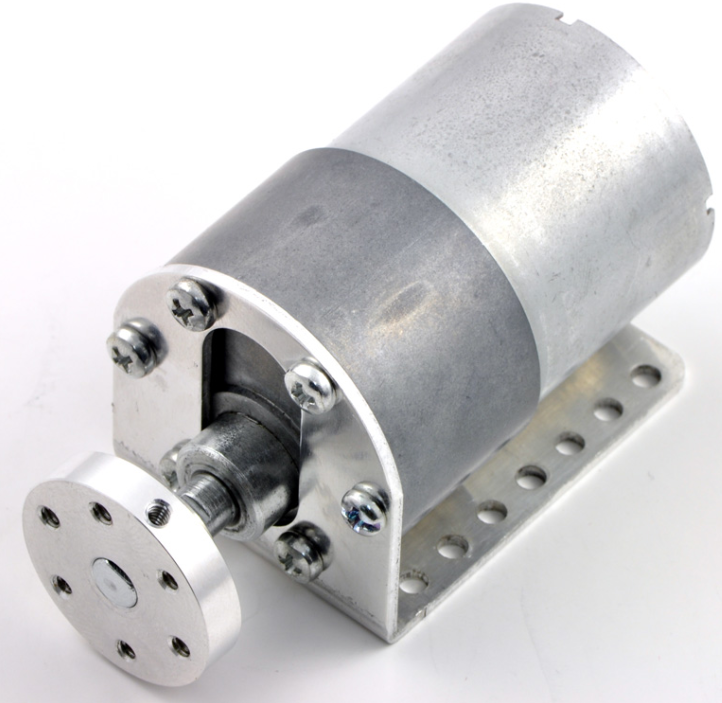
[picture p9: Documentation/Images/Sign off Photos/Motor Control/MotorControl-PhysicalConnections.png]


Since each of the four wheels is a drive wheel [4], they are each connected to a motor. The top photo shows that the wheel will be connected to the motor through a hub [5] with three screws. Each motor will have a mount [6] connecting it to the chassis. The mount will attach to the motor by six screws, as shown in the second photo, and this is attached to the chassis by four screws. The connection to the chassis is established in that subsystem's documentation.

## Analysis
### Acceleration

The robot must go 2 ft/s (0.6096 m/s) at its fastest speed. The worst-case scenario for this would be if it is at the maximum weight capacity and going up a 25-degree incline. 

$v = 0.6096\ m/s$ 

$a = \frac{v - v_{o}}{t}$

$a = \frac{0.6096 - 0}{1}$

$a = 0.6096\ m/s^2$

#### Subsystem Mass

$M_{Motors} \approx 0.840\ kg$

$M_{Microcontroller} \approx 0.037\ kg$

$M_{Motor Mount} \approx 0.044\ kg$

$M_{Wheels and Couplings} \approx 0.392\ kg$

$M_{Total Subsystem Weight} \approx 1.313\ kg$
$\ $

#### Maximum Robot Weight and Mass

$W_{Maximum} = 20.00\ lb$

$M_{Maximum} = 9.07\ kg$
$\ $
### Torque

$r = 0.030\ m$

$N = 4\ number of drive wheels$

$theta = 25\ degrees$

$e = 50\ efficiency$

$g = 9.80\ m/s^2$

$T = \frac{100(a+ gsin(theta)) * M * r}{50N}$

$T = 0.64698\ Nm = 6.5951\ kgcm$

$\ $

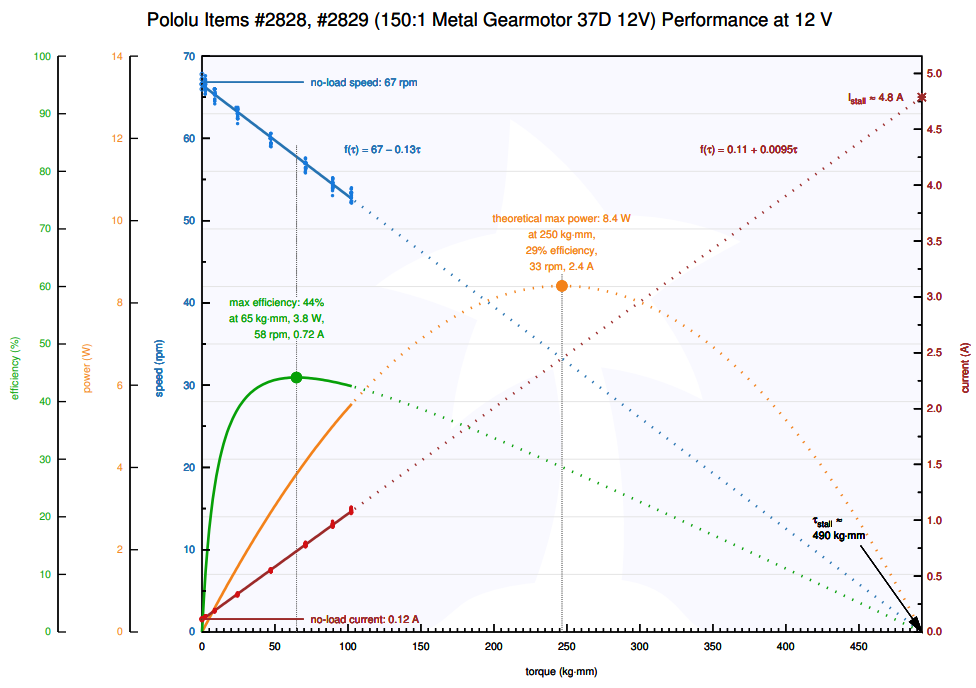
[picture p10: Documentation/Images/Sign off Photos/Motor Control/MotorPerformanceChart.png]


The chosen motor is the Pololu #2828. It is a 12V medium-power motor. The required torque for each motor is 6.5951 kg-cm. This motor has a max efficiency of 6.5 kg-cm of torque. At 6.5951 kg-cm of torque, the motor will operate at $\approx$ 99% of its maximum efficiency. This motor choice will allow the torque requirements to be met while simultaneously achieving high efficiency. The motor draws 0.72 A. The L298N motor driver supplies 2A, which is more than enough for this motor.

$6.5951\ kgcm / 10\ kgcm = 65.95$\%

$100$\% $- 65.95$\% $= 34.05$\%

At the current torque requirement of 6.5951 kg-mm of torque, only 65.95\% of the motor's torque capacity is being used. This allows for 34.05\% of each motor's torque capacity as the margin of safety.

## BOM
| Name of Item | Description | Part Number | Manufacturer | Quantity | Price | Total |
|---|---|---|---|---|---|---|
| Mecanum Wheels | The mecanum wheels allow the robot to move in any direction. | 14209 | Nexus Robot | 1  (set of 4)| 68.00 | 68.00 |
| Wheel Hubs | The wheel hub attaches a wheel to a motor. | 18077 | Nexus Robot | 4 | 6.90 | 6.90 |
| Motor | The motors will turn the wheels, allowing the robot to move. | 2828 | Pololu | 4 | 51.95 | 207.80  |
| Motor Mount | The motor mount attaches the motor to the chassis. | 2676 | Pololu | 2 (2 pack) | 9.95 | 19.90 |
| Motor Driver | The motor driver supplies the voltage and current to the motor. | L298N | STM electronics  | 4 | 11.63 | 46.52 |
| Microcontroller| The microcontroller communicates with the master control and motor drivers.  | Mega 2560 Rev 3 | Arduino | 1 | 48.40 | 48.40 |
| Total | | | | | Total Cost | $418.22 |

## References
[1] Microcontroller https://store-usa.arduino.cc/collections/boards-modules/products/arduino-mega-2560-rev3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 

[2] Motor Driver https://estore.st.com/en/l298n-cpn.html

[3] Motor https://www.pololu.com/product/2828

[4] Mecanum Wheel https://ozrobotics.com/shop/60mm-aluminum-lego-compatible-mecanum-wheel-set-2-left-2-right-basic-14159/

[5] Wheel Hub https://ozrobotics.com/shop/6mm-aluminum-mounting-hub-for-60mm-mecanum-wheel-18021/

[6] Motor Mount https://www.pololu.com/product/1084

Motor Sizing Tool used to double check calculations: https://community.robotshop.com/blog/show/drive-motor-sizing-tool

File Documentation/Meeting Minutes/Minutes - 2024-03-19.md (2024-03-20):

# Group 7 Advisor Meeting Minutes 24-03-19

## Attendance:

**In-Person:**\
Mabel Olson\
Reid Crews\
Luke Chapman\
Abigail Kennedy\
Isaac Hoese\
Isaac Jennings

**Remote:**\
Nan Chen

## Team Member Updates

Team members continued working on subsystems.

## Action Items from Last Meeting

Go over progress on subsystems.

## Meeting Minutes

Went over progress on subsystems. Sensor issues have now been fixed. The issue was that both I2C buses needed to be connected to 3.3 V rail to match the Arduino I2C output.

## Action Items for Next Meeting

Go over progress on subsystems, discuss anything needed for experimental analysis.

## Member Assignments

Continue working on subsystems.

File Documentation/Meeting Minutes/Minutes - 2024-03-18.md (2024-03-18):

# Group 7 Meeting Minutes 24-03-18

## Attendance:

**In-Person:**\
Mabel Olson\
Reid Crews\
Luke Chapman\
Isaac Jennings\
Isaac Hoese\
Luke Chapman

**Remote:**\

## Team Member Updates

Isaac H and Reid:\
Sensors work until the ToF sensors are connected. Since the ToF sensors are for object detection which isn't a constraint, we will discuss with Chen and Roberts about not integrating them since they are not necessary. Need to calibrate orientation sensor. Received new grove connections with grove-to-male pin and male-to-male pin adapters.

Abigail:\
Looked online to see if anyone has had similar issues with the motors. Haven't found anything yet. Will work on integrating with Isaac J on Thursday.

Isaac H:\
Got proof of concept for the serial communication. There is a python package for serial communication that should integrate pretty seamlessly with ROS. Will be meeting with everyone this week to integrate communications.

Mabel:\
Worked on rewiring the robot and labeling them. Will work on the redesign of the ultrasonic sensor attachment this week along with a few other miscellaneous changes. Also will work on some reach goals such housing for the switch and LCD screen. If time allows, may make a box to put over the top of the robot.

Luke:\
Soldered together another board, made a twisted pair cable for the battery charger to make charging during use easier. Didn't get a chance to to work on CPT, need to have someone show how to use the "blue box" amplifier before use.

## Action Items from Last Meeting

Go over progress on subsystems.

## Meeting Minutes

For comm to the motors, will send 2 bytes. MSB is linear velocity, second is angular velocity - pos in cw, neg is ccw.

## Action Items for Next Meeting

Go over progress on subsystems.

## Member Assignments

Continue working on subsystems.

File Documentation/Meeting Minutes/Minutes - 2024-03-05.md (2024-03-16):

# Group 7 Advisor Meeting Minutes 24-03-05

## Attendance:

**In-Person:**\
Abigail Kennedy\
Mabel Olson\
Reid Crews\
Isaac Hoese\
Luke Chapman\

**Remote:**\
Isaac Jennings\
Nan Chen

## Team Member Updates

Isaac and Reid have made progress on debugging the sensor readout. The issue is that some of the sensors are blocking some of the others for some reason. Will continue debugging to find more specifically what the issue is.

## Action Items from Last Meeting

Go over progress on subsystems, particularly the integration of the sensors and master control code on the Jetson Nano, and the communication between the microcontrollers.

## Meeting Minutes

Discussed with Dr. Chen about progress on subsystems. Discussed procedure for testing for the experimental analysis deadline and about the plan for wireless charging experimentation.

Ask Roberts about if Advisor need to check of experimental analysis and if due date is behind a week.

Ask Roberts about updating designs in the Github.

Agenda for tomorrow:
- Ask about experimental analysis date
- Ask about updating designs in GitHub
- Ask about pull-up resistor I2C + PCB

Miscellaneous note: It was agreed last meeting that for the 12 V rails, while the color code is orange, orange striping is also acceptable to make it easier to make the larger gauge wires orange if the original color is red.

## Action Items for Next Meeting

Go over progress on subsystems.

## Member Assignments

Continue working on subsystems, start working on subsytem parts of manual and think about experimental procedure.

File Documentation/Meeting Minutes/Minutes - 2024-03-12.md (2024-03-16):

# Group 7 Meeting Minutes 24-03-15

There were no meetings this week due to spring break.

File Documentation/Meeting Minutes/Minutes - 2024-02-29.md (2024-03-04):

# Group 7 Advisor Meeting Minutes 24-02-29

## Attendance:

**In-Person:**\
Isaac Hoese\
Isaac Jennings\
Mabel Olson\
Reid Crews\
Luke Chapman\
Abigail Kennedy\
Nan Chen

**Remote:**\

## Team Member Updates

Discussed with Roberts about several points on Monday and in class on Wednesday.

Everything needing to be in ROS.\
No, we can have some in Arduino.

Vin pin being ok with 5V.\
It is probably fine.

Speed not being 2 ft/s.\
Should debug and try to find out why it is not hitting 2 ft/s and fix it. If not, at least have a hypothesis for why it is not reaching that speed.

Emergency Stop Button Height.\
Try putting button on its side. Can also use another button that is not safety rated but stays pressed.

Technical Presentation Due Data.\
Current due date should be correct with the extra snow week, but the date can be debated if there is a reason for it.

## Action Items from Last Meeting

Go over the minimally functional prototype checklist with Dr. Chen.

## Meeting Minutes

The team demonstrated the minimally functional prototype with everything working. The sensor readout worked over wired connection, but the extra goal of having sensor readout over bluetooth did not work during the test, but a video of it working yesterday was shown to Dr. Chen.

The checklist can be found in the "Documentation/Minimally Functional Prototype" folder here on the repository along with videos of demonstrations showing a functioning minimally functional prototype.

## Action Items for Next Meeting

Go over progress on subsystems, particularly the integration of the sensors and master control code on the Jetson Nano, and the communication between the microcontrollers.

## Member Assignments

Continue working on subsystems.

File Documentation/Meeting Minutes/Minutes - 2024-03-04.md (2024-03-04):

# Group 7 Meeting Minutes 24-03-04

## Attendance:

**In-Person:**\
Isaac Hoese\
Isaac Jennings\
Reid Crews\
Mabel Olson\
Abigail Kennedy\
Luke Chapman

**Remote:**\

## Team Member Updates

Abigail:\
Reconnected motors. Measured motor driver voltages and found that they were at 10 V, not 12 V. Not sure why but will look into.

Isaac J:\
Found another problem that came up. The microsd card said that there was only 32 GB total of space because was being reformatted to only 32 GB, but got it reformatted to the full 256 GB. Figured out we're going to be using microROS and will be setting that up.

Reid:\
Tested the position and TOF sensors and got those working together. Goals are to extend the wire length.

Isaac H:\
Reid and Isaac integrated code together and got it working. Something is blocking Isaac's sensors, so will need to look into that.

Mabel:\
Redesigned some TOF and ultrasonic sensor attachments that should be better for going up inclines, probably wont use this version of the ultrasonic. Got everything below the height requirement. Will work on changes that Mabel and Reid talked about by making the TOF sensors at an angle, finalizing layout, and cleaning up wiring. Asked for people to give pin numbers for connections.

Luke:\
Added more connectors to power board and rewired button/switch with Mabel. Will start looking at CPT and making a twisted pair "cable" with alligator clamps for charging.

## Action Items from Last Meeting

Go over progress

## Meeting Minutes

People need to start finalizing layouts, so let Mabel know if anything needs to be moved.

Measures of success:

- [x] 1. Start button
- [x] 2. Allocated data input point for alternative 
- [ ] 3. Robot is autonomous
- [x] 4. Robot shall contain modules that are plug-and-play adaptable
- [x] 5. Robot shall possess robust, centralized, charging system
- [ ] 6. Wireless charging will be evaluated
- [x] 7. Emergency stop button
- [x] 8. Power bus not inhibited by DC motor operation
- [ ] 9. Shall be able to travel up inclines of 25 degrees
- [ ] 10. Turn 360 degrees, forwards, backwards, based on input from sensors
- [ ] 11. Navigation system that controls movement
- [ ] 12. Know location within 2 inch tolerance
- [ ] 13. Max speed of 2 ft/s
- [ ] 14. User manual
- [x] 15. Not use radiative WPT
- [ ] 16. Shall abide by FCC standards
- [ ] 17. Shall abide by NEC.xx 
- [x] 18. Shall abide by IEEE code of ethics

## Action Items for Next Meeting

Go over progress and experimentation.

## Member Assignments

Continue working on subsystems

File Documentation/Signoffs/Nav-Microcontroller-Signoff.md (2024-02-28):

# Navigation Microcontroller Signoff

## Functionality
The microcontroller susbystem will provide the computing power needed to read in sensor data, filter the data as needed, and send the resulting values to the master control subsystem via serial communication. The data in the master control will help navigate the robot across the arena.

## Reach Goals

There are two reach goals in the project. The first is the implementation of the ESP 32 wifi module. The implementation will require 2 sets of the ESP 32 boards. One will act as a receiver and one will act as a transmitter. The transmitter will be embedded in the robot. The module will be connected to the Arduino navigation microcontroller and will send sensor data to the receiver in various intervals (update). The receiver will be conencted to a pc to display the data via a serial monitor.
	Because the ESP uses wifi, the transmission speed should not be an issue. A determined updating rate will be used based on the updating needs. A possible update speed is 100 Hz. This should provide the data to be updated close to real time.
The second reach goal is an on-robot OLED display. The display will aid teams in troubleshooting, as well as the option of showing the robot's battery life.

***The implementation of reach goals will only occur if it is evident that the requirements provided by the customer are met, or will be met.***

## Constraints

### Derived from Shall Statements
- C4: The robot shall contain modules that are plug-and-play adaptable for different IEEE competition requirements.
	- This applies to the microcontroller subsystem because the bus connections must be easily replaceable or removable. The microcontroller code must also be easily adaptable.

* C11: The robot shall have a navigation system that controls movement.
	* The microcontroller subsystem will transmit the data from all navigation sensors to the master control. The master control will make decisions based off of the provided data.

### Derived from Broader Implications
	
- C14: The robot shall have a user manual that explains all functions and capabilities of the robot. 
	- The microcontroller connections and coding techniques will be documented to make it easily adoptable for future Capstone teams.

## Schematics
### Arduino Pinouts
<p align = "center">
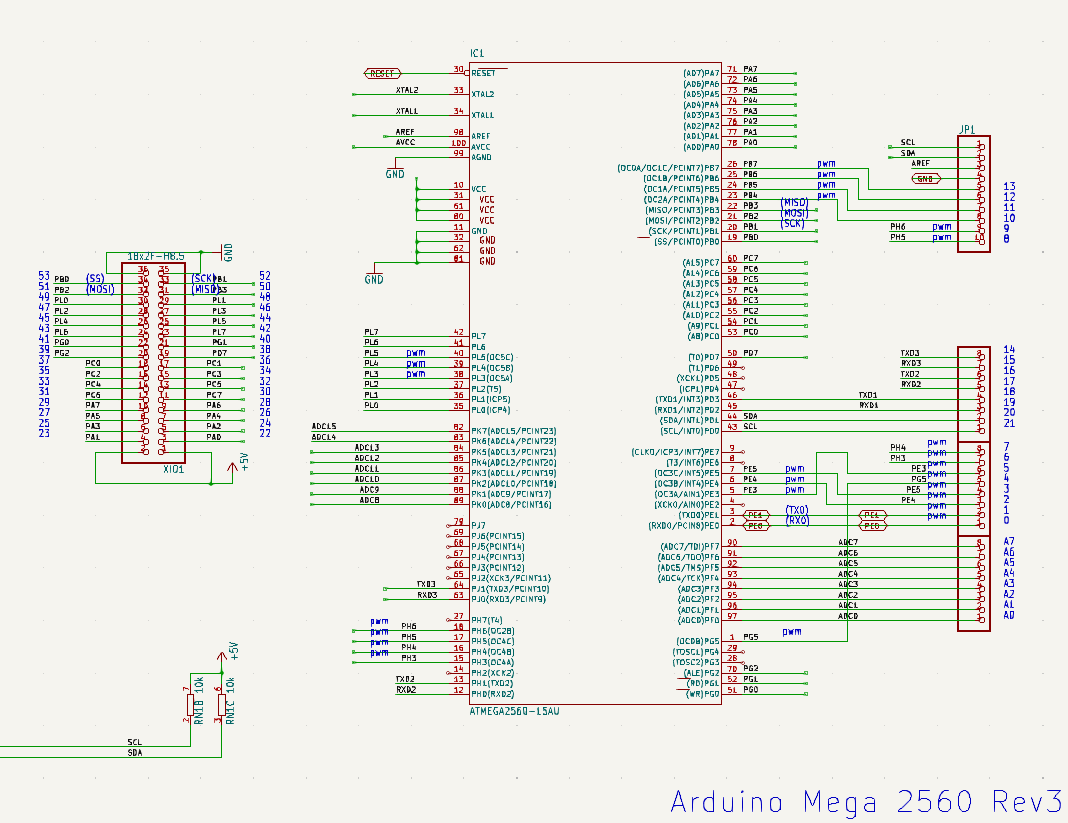
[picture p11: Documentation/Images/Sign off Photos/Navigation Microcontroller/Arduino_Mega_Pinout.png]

</p>

The pinout diagram of the Arduino Mega 2560 Rev3 board is shown above. The electrical connections for sensors and other modules will be discussed in the following schematic sections. A pinout table will be provided at the end of the schematics section to provide connection documentation.

### Grove Connections
<p align = "center">
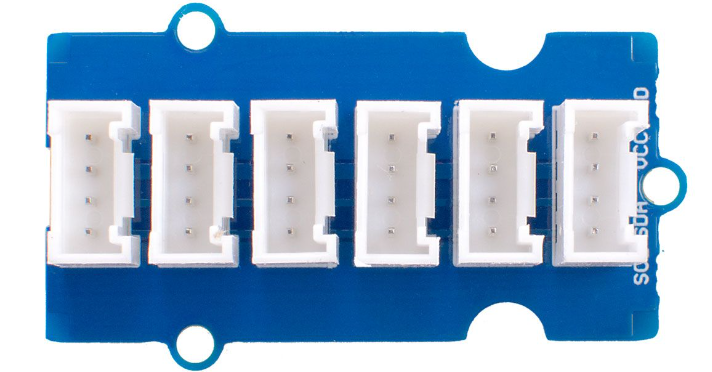
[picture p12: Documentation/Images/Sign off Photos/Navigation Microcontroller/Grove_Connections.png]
Grove Bus

</p>

The I2C bus will be implemented using 4 Grove I2C Hub 6 Port modules. The first connection to each of the modules will be the SCL an SDA pins of the Arduino. The power and ground pins will be connected directly to the regulated bus to prevent the Arduino from sourcing too much current. Two of the four modules will be connected to the 5V power bus while the other two will be connected to the 3.3 V bus. The 5 V and 3 V connections will power all electronic sensors. The bus will allow all I2C compatible sensors to be read in with just 2 Arduino pins. By using the grove bus, every I2C sensor will be 100% plug and play adaptable. 

<p align = "center">
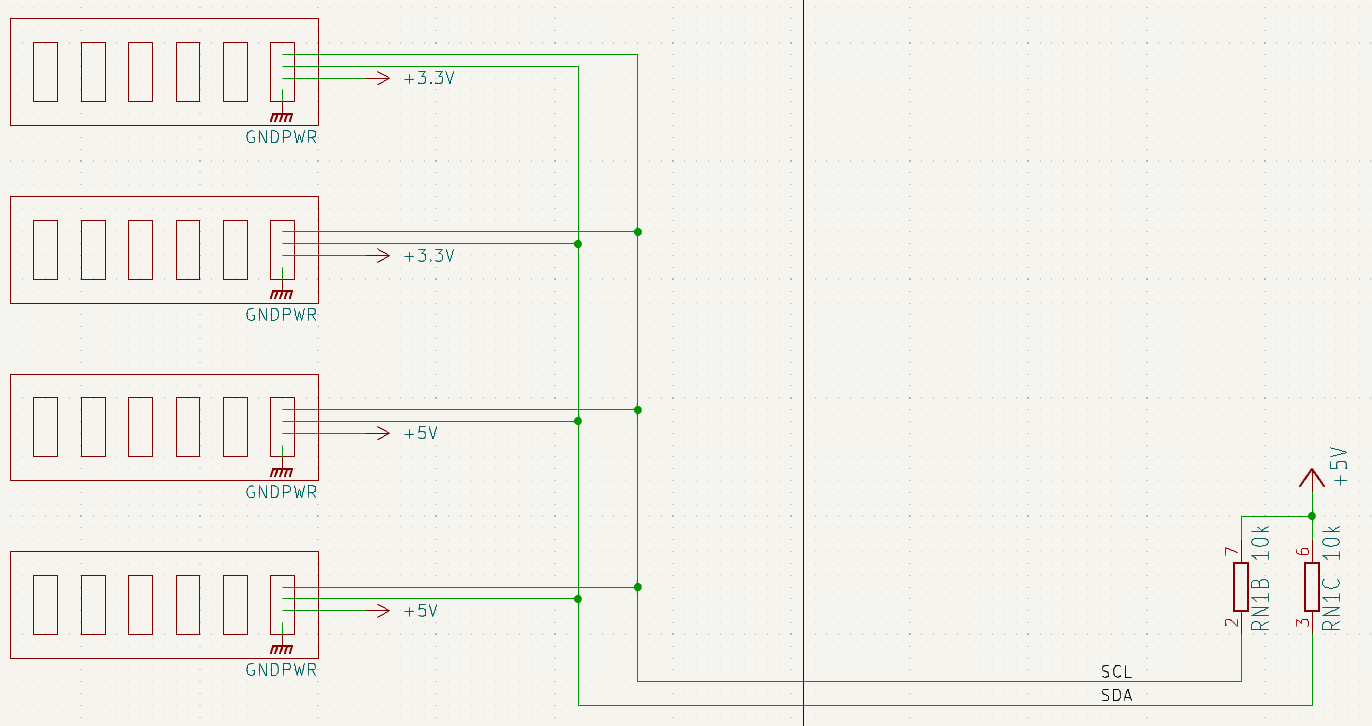
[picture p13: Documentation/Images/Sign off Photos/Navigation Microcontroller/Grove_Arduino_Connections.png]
Grove-Arduino

</p>

### Sensor Connections

<p align = "center">
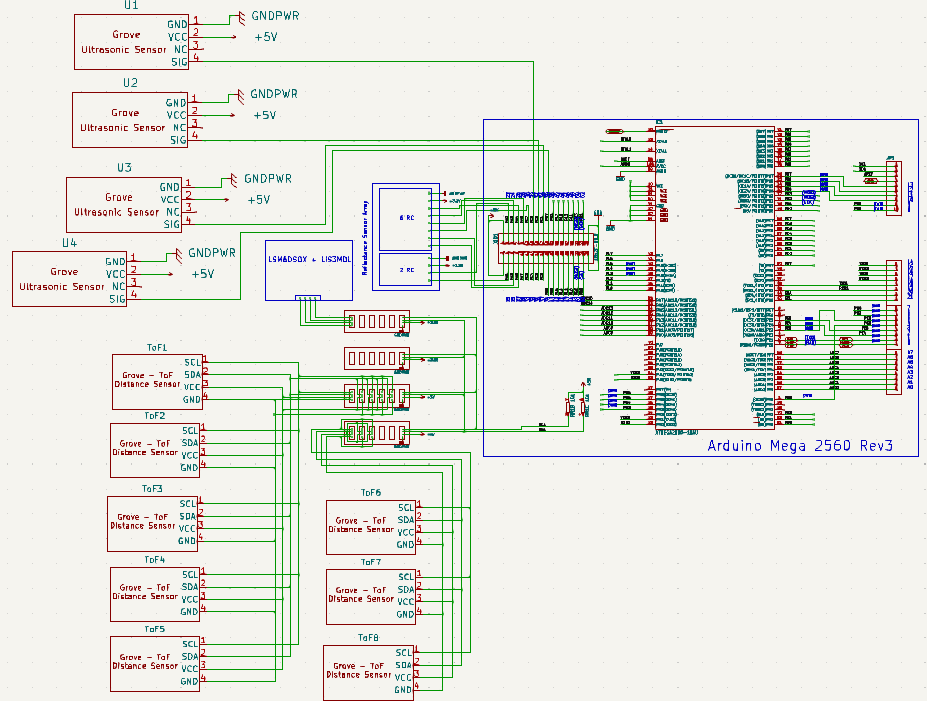
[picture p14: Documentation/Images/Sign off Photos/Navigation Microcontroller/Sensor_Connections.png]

</p>

## Analysis

### Arduino Analysis
The Arduino Mega 2560 Rev3 has 54 digital pins and 16 analog pins. It also has 15 PWM output pins. The PWM pins will give future teams the option to attach servo or stepper motors to complete their tasks without having to implement another microcontroller. The Mega has 4 sets of Tx/Rx pins for UART communication. In addition to the UART pins, there are SDA and SCL pins for I2C communication. The microcontroller has an additional 4 kb of EEPROM that does not get erased from powering down. 

The input/supply voltage to the Arduino Mega can span from 7 to 12 V from the DC jack and the VIN pin. Powering through the USB has a range of 4.8 to 5.5 V, but since the communication from Mega to Jetson Nano will use the USB for data transmission, this is not an option for powering the microcontroller.

The Arduino serial monitor and serial plotter will aid in validating the voltages received from the sensors. The plotter will also aid in creating software filters. Each of the sensors will be tested with the plotter active so that votlage readings are known for a controlled reading. 
### Arduino Libraries
The sensor sets used for the robust robot will utilize manufacturer provided Arduino Libraries to ease the coding process.

Line Following Library: [QTR Sensors][def3]

Orientation Library: [Accelerometer][def4] , [Compass][def5]

Position Library: [Grove - Ultrasonic Ranger][def2]

Object Detection Library: [Grove - Time of Flight Distance Sensor VL53L0X][def1] 

[def1]: https://github.com/adafruit/Adafruit_VL53L0X

[def2]: https://github.com/SeeedDocument/Grove_Ultrasonic_Ranger

[def3]: https://www.pololu.com/docs/0J19/1

[def4]: https://github.com/adafruit/Adafruit_LSM6DS

[def5]: https://github.com/adafruit/Adafruit_LIS3MDL

### Communication with Jetson Nano
The Arduino will communicate with the Jetson Nano through the USB port. The USB port will provide serial data to the Jetson Nano using UART (Universal Asynchronous Receiver Transmitter) Communication Protocol. Another option is to use the Tx/Rx pins on the Arduino Mega to send the serial data, rather than the USB. This would allow code to be uploaded to the Arduino Mega while still being serially connected to the Jetson Nano.

By using UART, the serial data must have a beginning marker, such as '<', and an ending marker, such as '>'. This is an effect of the communication method being asynchronous. The start and end markers will allow the Jetson Nano to differentiate the data packages.

### Reach Goal Analysis

#### ESP 32
The ESP 32 module is an MCU created by Espressif. Adafruit's "Huzzah32" breakout board will provide the system with communication from robot to user. The IEEE competiton strictly prohibits the use of external control. Therefore, the module will be easily removable for the competition. The ESP 32 will be heavily used in testing so real-time data can be read while the robot works autonomously. The module is SPI, UART, and I2C compatible. The module has an on-board antenna and supports both wifi and bluetooth for wireless communication. The ESP 32 has an operating voltage range from 3.0 to 3.6 V, making it compatible with the 3.3 V distribution bus present in the robot. Because this is a reach goal, the 0.5 A draw is not accounted for on the power distribution anaylsis. Thus, a small battery just for the ESP 32 would be the best route if implemented.

**NOTE: Getting devices approved for TTU wifi usage may be an issue, so the bluetooth attribute will likely be used.**

#### OLED Display
The SSD 1306 0.96" display has a 128 x 64 dot matrix for display. The module runs off of 3.3 V and has a maximum operating current of 15 mA. The module is I2C compatible and can be easily implemented into the data bus by using a grove to male pin wire. Because it is an OLED, user-created images can be imported and used. This will aid in showing battery life pictures such as the one seen below: 

<p align = "center">
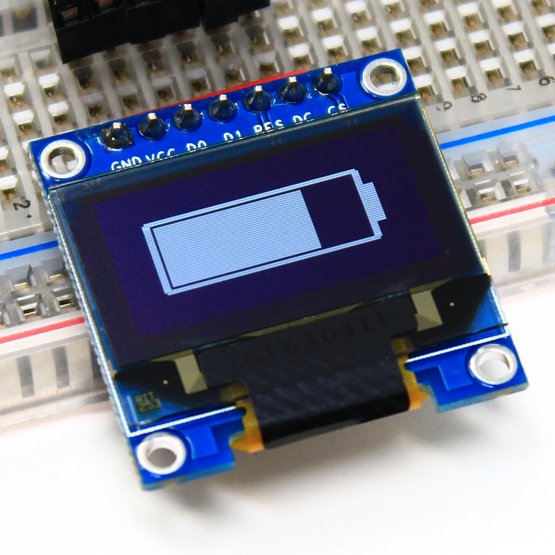
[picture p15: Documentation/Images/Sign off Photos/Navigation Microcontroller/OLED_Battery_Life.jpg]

</p>

### Coding Conventions

To keep code looking uniform, the coding conventions brought forth by Dr. Bruce will be used. The coding convention documentation can be found here: http://jwbruce.info/teaching/ece4140/files/ccode.pdf. The convention covers variable, struct, and class naming, as well as commenting techniques.

## Robot Integration

The Arduino Mega and I2C bus will be attached to the robot via 3D printed trays. The trays will be in the interior of the robot. The ESP 32 will have it's own tray if adopted. The tray must be easily accessible so that wiring can be disconnected for the competition. The OLED display will be mounted on an external wall of the robot where it can be easily viewed.

## BOM
|Item |Quantity |Price |Total |
|---|---|---|---|
|Arduino Mega|1 |\$ 43.56 $^{1}$ |$43.56|
|Grove I2C Bus|4 |$1.70|$6.80|
|ESP 32 $^{2}$ |1| $19.95| $19.95|
|OLED Display $^{2}$|1 |$8.99|$8.99
Subsystem Total |||$50.36|

1. This is a sale price listed on Amazon. Normal retail is $55.00
2. Reach goals
   
## References
Arduino Mega Datasheet: https://docs.arduino.cc/resources/datasheets/A000067-datasheet.pdf

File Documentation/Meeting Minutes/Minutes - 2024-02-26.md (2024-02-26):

# Group 7 Meeting Minutes 24-02-26

## Attendance:

**In-Person:**\
Abigail Kennedy\
Mabel Olson\
Luke Chapman\
Reid Crews\
Isaac H\
Isaac J

**Remote:**\

## Team Member Updates

Abigail:\
Came in Thursday, got motor code working, found out that there is a broken pin (4). 

Luke:\
Did testing on the battery, power board, and motors. Everything works as expected. Notes taken can be found in /Electrical/Testing.

Isaac J:\
Got the ROS downloaded on the Jetson Nano. Will be running an older version of ROS because the Jetson Nano runs Ubuntu 20. 

Isaac H:\
Need to add GUI support for Reid's sensors and add to board.

Mabel:\
Printed more of the sensor mounts. Working on the sensor connector 3d printed mounts. Also, organizing the wires and layout of all of the components. Beginning to look at color coding.

Reid:\
Tested all of the ToF sensors with the shutdown pin. Tested with 3 at once and it worked, and then added code to Isaac's codebase.

## Action Items from Last Meeting

Go over progress on MFP. 

## Meeting Minutes

Going over MFP checklist. We basically have everything working and are on track to having the MFP ready on Thursday.

Discussing wire color coding.

Orange - 12 V
Red - 3.3/5 V
Black - GND

Sensor connections will be device-specific.

## Action Items for Next Meeting

Demonstrate the MFP with Dr. Chen.

## Member Assignments

Continue working on subsystems.

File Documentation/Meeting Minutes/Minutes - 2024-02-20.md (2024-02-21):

# Group 7 Meeting Minutes 24-02-20

## Attendance:

**In-Person:**\
Mabel Olson\
Reid Crews\
Isaac Hoese\
Abigail Kennedy\
Luke Chapman\
Nan Chen

**Remote:**\
Isaac Jennings

## Team Member Updates

Team members continued working on subsystems. The metal motor mounts were fabricated and the base of the robot has been put together.

## Action Items from Last Meeting

Go over progress on MFP.

## Meeting Minutes

Discussed meeting times with Chen.

Planning to meet 3-4 on Thursday like normal for showing the MFP, but will make plans for a later date if we cannot have it done by then.

No meeting Tuesday 3-4 with advisor so that we can have our MFP meeting on Thursday.

Will ask Roberts tomorrow if there is anything we need to turn into the dropbox on iLearn for the MFP.

Should print out the MFP checklist and check off what is done. 

## Action Items for Next Meeting

Go over progress on MFP and if checklist will need to be negotiated on.

## Member Assignments

Continue working on subsystems.

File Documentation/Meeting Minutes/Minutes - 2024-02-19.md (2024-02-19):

# Group 7 Meeting Minutes 24-02-19

## Attendance:

**In-Person:**\
Abigail Kennedy\
Mabel Olson\
Reid Crews\
Isaac Hoese\
Isaac Jennings\
Luke Chapman

**Remote:**

## Team Member Updates

Mabel:\
Motor mounts have not been cut yet, but are supposed to be worked on today.

Luke:\
Soldered most of a second board and diodes on the older board. Started looking at battery life monitoring. 

Abigail:\
Did some work on the motor code

Reid:\
Worked on the ToF sensors and will test to make sure that all of them work.

Isaac H:\
Got the GUI for all of the sensors working. Go the pins for the line-following soldered.

Isaac J:\
Still working on getting everything connected together. Should be up by next week to be able to work with all of the different components talking to each other.

## Action Items from Last Meeting

Go over progress made on subsystems.

## Meeting Minutes

Team members went over what they did 

## Action Items for Next Meeting

Go over any subsystem progress and make agenda.

## Member Assignments

Continue working on subsystems.

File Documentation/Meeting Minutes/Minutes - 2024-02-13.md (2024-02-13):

# Group 7 Advisor Meeting Minutes 24-02-13

## Attendance:

**In-Person:**\
Abigail Kennedy\
Reid Crews\
Mabel Olson\
Isaac Hoese\
Luke Chapman\
Nan Chen

**Remote:**\
Isaac Jennings

## Team Member Updates

Team members working on their subsystems.

## Action Items from Last Meeting

Discuss progress with Dr. Chen. Make agenda for tomorrow.

## Meeting Minutes

Motor mounts are being cut out of metal instead of plastic because plastic has not been strong enough.

Dr. Chen agreed that for the "third board" as long as we can demonstrate functioning line following that would be sufficient.

Making agenda for tomorrow:
- Updates about motor mounts
- 2022 Board is not in capstone lab

## Action Items for Next Meeting

Go over progress made on subsystems.

## Member Assignments

Continue working on subsystems.

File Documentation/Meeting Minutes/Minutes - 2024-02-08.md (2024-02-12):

# Group 7 Advisor Meeting Minutes 24-02-08

## Attendance:

**In-Person:**\
Reid Crews\
Abigail Kennedy\
Isaac Hoese\
Luke Chapman\
Mabel Olson\
Nan Chen

**Remote:**\
Isaac Jennings

## Action Items from Last Meeting

Go over what all of the team members have done. Discuss with Dr. Chen  about the MFP.

## Meeting Minutes

Going over previously made checklist for MFP.

Remaining MFP checklist:

- Start button/switch
- Be able to move the motors
- Easily connectable power buses for voltages
- Sensor connections easily changeable
- Proper voltages from power buses
- E Stop button
- ESP bluetooth communcation to show sensor data

Check if Tuesday at 3pm works for everyone for a different advisor capstone meeting time.

## Action Items for Next Meeting

Discuss progress and issues faced by team members

## Member Assignments

Continue working on subsystems.

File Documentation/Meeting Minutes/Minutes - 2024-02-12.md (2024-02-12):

# Group 7 Meeting Minutes 24-02-12

## Attendance:

**In-Person:**\
Reid Crews\
Isaac Jennings\
Abigail Kennedy\
Mabel Olson\
Isaac Hoese\
Luke Chapman

**Remote:**\

## Team Member Updates

Abigail:\
Worked on the code for the motors, waiting for the motor mounts to be finished before beginning all of the motor testing.

Isaac J:\
Missing a cable, when that comes should be able to get microcontroller comm working. Got robot simulation working with a controller. Will get robot working first with a keyboard then a controller.

Reid:\
Got two time-of-flight sensors working together, needed to solder in a shutdown pin. Had to use the Adafruit library for the sensors because some of the other library is private.

Isaac H:\
Worked on wireless communciation and started trying to get the UART orking. Did a line following test which failed bc of the opacitity of the paper, redoing with duct tape on paper.

Mabel:\
Met with the people in the Machine shop and they said they can probably do the motor mounts. The shop said they would do water jet cutting and have metal that is about the right thickness. Redid the motor mount models and reduced to one attachment point per side so thtat it can be slid further forward and backwards. Redesigned the attachment model to add a back panel for easier mounting and sent to library for printing. Going to meet with the machine shop today about getting the new attachment models fabricated. 

Luke:\
Finished the testing able to be done right now, board can do 5 A with no problem, but the power supply drops the voltage when the current output is turned on. The next step in testing is to test the board with the motors when the motors are ready. Soldered several more connectors, sockets and screw terminals, that are ready for use. Also connected the emergency stop button to the robot.

## Action Items from Last Meeting

Go over what each team member has done on their subsystems.

## Meeting Minutes

Advisor meetings will now be at 3pm on Tuesday.

The team went over the progress that everyone had on their subsystems and discussed plans going forward. It seems that the hardware-side of the project will likely be done before the software-side. The final testing of the power board is waiting on the motor control to be completed, which is waiting on the new motor mounts to be completed, which in turn is waiting on the machine shop to fabricate them. 

## Action Items for Next Meeting

Go over what each team member has done on their subsystems. 

## Member Assignments

Continue working on subsystems.

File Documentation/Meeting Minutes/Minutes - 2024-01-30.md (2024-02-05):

# Group 7 Meeting Minutes 24-01-30

## Attendance:

**In-Person:**\
Reid Crews\
Mabel Olson\
Abigail Kennedy\
Luke Chapman\
Isaac Hoese\
Nan Chen

**Remote:**\
Isaac Jennings

## Action Items from Last Meeting

Make agenda for meeting with Roberts on Wednesday.

## Meeting Minutes

Advisor Meeting:

The team went through the detail design document to develop the guidelines for our minimally functional prototype.

- Start button
- Be able to move the motors
- Easily connectable power buses for voltages
- Sensor connections easily changeable
- Proper voltages from power buses
- E Stop button
- Basic robot mobility - forward, backward, rotate
- Robot can go up an incline
- Robot can know its approximate location within a two-inch tolerance
- 2-Way communication between the Jetson Nano and auxilliary controllers

Changing minimually function prototype due date to 2/27/24 so that it is on a date that we will be meeting.

The team is giving itself a deadline to have everything put together by a week before the minimally functional prototype.

Agenda for Wednesday Meeting:

- Ask Roberts about what he expects from a minimally functional prototype
- Ask Roberts about the process for ordering a new PCB if necessary

From Roberts:

Everything is wired but it might do almost nothing. Does something non-trivial. Going up incline may be a little too much to expect for the minimally-functional design. Ex: Sensor is plugged up and communicating, even if the communication is incoherant. 

Minimally functional design deadline is not negotiable, the content is.

Can negotiate on minimally functional design parameters (e.g. Trade higher functionality in program for less functional motors). 

## Action Items for Next Meeting

Go over what everyone has done since the last meeting. Add more specific objectives for next meeting based on progress/issues from last meeting.

## Member Assignments

Isaac J:\
Start working with Nav2 (ROS navigation package) and learning how to navigate the robot. Will also start on a more detailed flowchart for how the robot structure will work.

Luke:\
Respond to whatever changes Dr. Chen requests on the wireless charging signoff. Continue debugging the power board to ensure that it can provide the correct output voltages and currents. Also testing the input voltage range. Finally, make sure that the battery charger can successfully charge the battery.

Abigail:\
Will start looking at the motors and how the encoding works. Start working on the skeleton code for the motor control.

Mabel:\
Look over all of the prints from last semester and make sure that everything fits together.

Isaac H:\
Work more on the line following, testing with different colors to see if the reflectances change and if any amplification needs to be done in code. Also work on the OLED display to be put on the robot. Will make the line-following code more modular.

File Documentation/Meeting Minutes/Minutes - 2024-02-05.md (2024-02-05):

# Group 7 Meeting Minutes 24-02-05

## Attendance:

**In-Person:**\
Mabel Olson\
Abigail Kennedy\
Luke Chapman\
Reid Crews\
Isaac Jennings\
Isaac Hoese

**Remote:**\

## Team Member Updates

Mabel:\
Got more of the components printed, everything except for a few sensor attachments. Printed using Van Neste's printer using resin due to printer's being out of order. Submitted things to be printed at the library last week and has not been printed yet. Will send email to VN to print other stuff.

Isaac H:\
Worked a lot on the line sensor. Found out that the library the sensor uses does nto actually work with the arduino library.Will do line following testing Tue or Wed. Need to find out how to interface with the two sensors. Will also work on the bluetooth connectivity

Reid:\
Got TOF sensor to work and got code for the ultrasonic sensor to work. Will try doing two TOF sensors and see if need to change the code for them. 

Luke:\
Did testing on the power board. Tested to make sure board works over the entire battery range, made sure the battery charger works with the battery and the board can be powered with the battery and charger connected. Also tested the short-circuit protection of the charger, which worked fine. Notes from testing are in the "Documentation/Electrical."

Isaac J:\
Looked in to the navigation stack to add nav to the code and figure out what the control diagram and structure is going to look like. There is a nice sensor library that can be used. The largest unknown is to figure out how to use ROS on the arduinos. Can do all of the sensor code with this library and the library takes care of a lot of the specific details. Will probably use the "Twist" function of ROS for motor communcation.

Abigail:\
Worked on the motor code to get basic modular commands to getting the robot to be able to move forward, backward, and rotate. Also put the motors on the robot, they all sit fine except for one that is missing a piece. Will simplify the code this week and test to make sure that it works fine while attached to the robot.

## Action Items from Last Meeting

Go over what everyone has done since the last meeting. Add more specific objectives for next meeting based on progress/issues from last meeting.

## Meeting Minutes

Should mention to Roberts about the week we lost and see if the prototype deadline should be pushed back a week. 

Need to figure out meeting time with Dr. Chen so that we can talk to her about the prototype now that we know more about what Roberts expects.

Mabel has found issues with the different tolerances and precisions of the different printers. The resin printers have been very good, one of the library printers is very good, and some of VN's printer have not been quite as good.

Meeting time discussion. The team found that 1:00pm-2:00pm Thursday works best of the times that Dr. Chen gave. Need to mention that Roberts' prototype is different from what we discussed.

Should make a checklist to be able to check off for the minimally function prototype (MFP). 

Agenda bullet points:
- Power Board testing
- Moving the prototype deadline
- Third SECON board

The team saw how most of the components would fit in the robot chassis.

## Action Items for Next Meeting

Go over what all of the team members have done. Discuss with Dr. Chen  about the MFP.

## Member Assignments

Continue working on subsystems.

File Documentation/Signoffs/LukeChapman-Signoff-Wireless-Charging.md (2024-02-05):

# Wireless Charging Signoff

## Functionality

The wireless charging subsystem will be more experimental than the other subsystems. The primary functionality of this subsystem is to supply power wirelessly to the robot over the entire arena area so that the battery can be charged during use and testing. This will be done using capacitive wireless charging, as it has the most potential to allow for wireless power transfer over the largest area.

## Constraints

### Derived from Shall Statements

- C6: Wireless charging shall be evaluated as an option for
charging the robot.
	+ This constraint was made at the request of the customer. This constraint requires that wireless charging be investigated as best as possible as a method of charging the robot wirelessly while the robot being used is in the game arena. The goal for this constraint is that the robot be able to be charged over as much of the entire 4 ft x 8 ft arena area as possible [1][2][3].

### Derived from Broader Implications

- C15: The robot shall not use radiative wireless power transfer
technology.
	+ This constraint rules out radiative wireless power transfer methods for wireless charging. Radiative wireless power transfer has a higher potential for personal harm than nonradiative and so has stricter regulations. Radiative wireless power can only be safely used for power consumption under 10 milliwatts, much less than the robot requirements, making radiative power transfer too dangerous of an option to pursue [4][5].

- C16: The robot shall abide by the applicable FCC regulations
regarding wireless charging methods outlined in parts 15
and 18 of the standard.
	+ This constraint requires that the wireless charging methods investigated and used comply with all FCC regulations for wireless power transfer in order to minimize risk of personal harm [4].

## Schematic

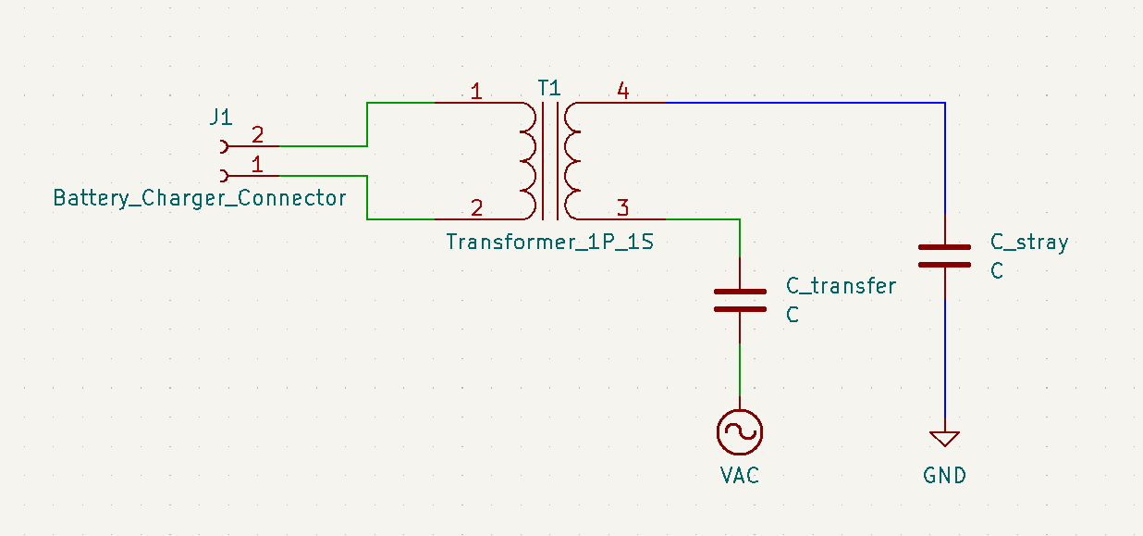
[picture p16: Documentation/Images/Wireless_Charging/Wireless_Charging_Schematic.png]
Capacitive Wireless Charging Schematic


This schematic is a simplified version of the schematic presented by Van Neste et al. in “Quasi-wireless capacitive energy transfer for the dynamic charging of personal mobility vehicles” and “Quasi-wireless surface power and control for battery-free robotics” [6][7]. 

In this setup, known as unipolar capacitive wireless power transfer, a metal plane is excited by a high-frequency function generator [6][7]. This capacitively couples to a metal plane on the robot, represented by C_transfer. This plane on the robot is put in series with the primary inductor of a transformer to step up/down the voltage to whatever voltage is needed by the charger on the secondary side. The other side of the primary inductor of the transformer has a stray capacitance that capacitively couples to the ground of the function generator, represented by C_stray on the schematic.

## Analysis

As mentioned above, this subsystem will be very experimental. Because of this, the analysis for this subsystem will consist mostly of reviewing existing literature on wireless power transfer and citing work already done for the subsystem design.

### Wireless Charging Evaluation

The two main technologies for wireless power transfer are inductive and capacitive transfer [5]. Both technologies have strengths and weaknesses that were evaluated for this subsystem. Inductive power transfer (IPT) utilizes two inductors to inductively couple to each other and transfer power from transmitter to receiver. IPT is more researched and widely used, but has a very short range as the transmitter and receiver become unaligned. Capacitive power transfer (CPT) uses capacitors to couple between transmitter and receiver, where one conductor is the transmitter and one is the receiver, forming a capacitive connection between the two. Two of these types of capacitors are required for a full current path. CPT also has a very short range, but large conductive sheets can be used for the transmitting half of the capacitor, allowing for a large surface area over which a device can wirelessly receive power [6][7].

It is for these reasons that capacitive power transfer was chosen to be explored in this subsystem. The goal is that the entire 4 ft x 8 ft area of the arena can have a conductive sheet underneath, allowing for wireless charging over the entire arena area [1]-[3].

The subsystem design is based primarily on the work done by Van Neste, a faculty member at TnTech, et al. in “Quasi-wireless capacitive energy transfer for the dynamic charging of personal mobility vehicles” and “Quasi-wireless surface power and control for battery-free robotics” [6][7]. This is because the applications of their technology are very close to our applications. In the first paper, the group uses CPT to have a large area over which a personal mobility vehicle can be charged, very similar to this subsystem [6].

In the personal mobility vehicle paper, the research group uses large sheets of aluminum foil for the large conductive planes used as capacitive transmitter and receiver [6]. This transmitting conductive sheet on the ground is excited by a function generator at several MHz and amplified by a high-powered RF amplifier. Aluminum foil will be purchased for this subsystem and function generators are readily available at TnTech facilities as well as the RF amplifiers used in this paper, which can be accessed through collaboration with Dr. Van Neste and his research group. In the future, designing an amplifier system may be investigated. The magnet wire will be purchased for construction of transformers for the CPT system.

### Not Using Radiative Wireless Power Transfer

The wireless power transfer used in this subsystem uses capacitive power transfer and uses no radiative power transfer methods or technologies [5][6]. This fulfills this constraint.

### Abiding by FCC Regulations

One of the primary differences between Dr. Van Neste's work and other CPT research is the use of unipolar power transfer as opposed to bipolar power transfer [6][7]. Unipolar CPT utilizes one major capacitor for the power transfer to the 

## BOM

| Item | Part Number | Quantity | Price/Unit | Item Price |
| --- | --- | --- | --- | --- |
| Aluminum Foil | Amazon Basics Aluminum Foil, 250 Sq Ft | 1 | $13.49 | $13.49 |
| Magnet Wire | 610222 | 1 | $120.57 | $120.57 |

## References

[1] “IEEE SOUTHEASTCON 2024 STUDENT HARDWARE COMPETITION RULES Version 5.6,”Sep.2023. [Online]. Available: https://ieeesoutheastcon.org/wp-content/uploads/sites/497/SEC24-HW-Competition_V5.6-1.pdf

[2] “IEEE SoutheastCon 2023 Hardware Competition Rules,” Oct. 2022. [Online]. Available: https://github.com/lchapman42/Control-Sensing-Wireless-Charging-Robot/blob/main/Documentation/Background%20Documents/IEEE%20SoutheastCon%202023%20Hardware%20Competit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

[3] “IEEE SoutheastCon 2022 Hardware Competition Rules,” Mar. 2021. [Online]. Available: https://github.com/lchapman42/ Control-Sensing-Wireless-Charging-Robot/tree/main/Documentation

[4] “RF EXPOSURE CONSIDERATIONS FOR LOW POWER CONSUMER WIRELESS POWER TRANSFER APPLICATIONS,” Jan. 2021. [Online]. Available: https://apps.fcc.gov/kdb/GetAttachment.html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

[5] X. Lu, P. Wang, D. Niyato, D. I. Kim, and Z. Han, “Wireless Charging
Technologies: Fundamentals, Standards, and Network Applications,”
IEEE Communications Surveys & Tutorials, vol. 18, no. 2, pp. 1413–
1452, 2016. [Online]. Available: https://ieeexplore.ieee.org/document/7327131

[6] C. W. Van Neste, A. Phani, R. Hull, J. E. Hawk, and T. Thundat, “Quasi-wireless capacitive energy transfer for the dynamic charging of personal mobility vehicles,” in 2016 IEEE PELS Workshop on Emerging Technologies: Wireless Power Transfer (WoW), Knoxville, TN, USA: IEEE, Oct. 2016, pp. 196–199. doi: 10.1109/WoW.2016.7772091.

[7] A. K. Pickering, R. Hull, J. E. Hawk, A. Phani, C. W. Van Neste, and T. Thundat, “Quasi-wireless surface power and control for battery-free robotics,” Wirel Pow Transfer, vol. 2, no. 2, pp. 134–142, Sep. 2015, doi: 10.1017/wpt.2015.15.

[8] “MW-28C Datasheet.” CNC Tech, Nov. 18, 2016. Accessed: Nov. 27, 2023. [Online]. Available: https://mm.digikey.com/Volume0/opasdata/d220001/medias/docus/1066/MW-28C_Spec.pdf

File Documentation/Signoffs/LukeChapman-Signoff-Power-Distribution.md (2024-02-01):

# Power Distribution Signoff

## Functionality

The primary functionality of the power distribution system is to reliably supply power to all of the components of the robot. The power distribution system can supply power through 3.3 V, 5 V, and 12 V rails, with the 12 V rails being dedicated for motor use.

## Constraints

### Derived from Shall Statements

- The power distribution system must be able to supply enough current and power to all other subsystems on the robot for their proper functionality.
    + This constraint was made because the purpose of the power distribution system is to provide adequate power the entire robot. Because of this, the other subsystems constrain the power distribution subsystem and this constraint is the most important to this subsystem.
- C1: The robot shall have a single start button. Once activated, the robot will begin navigating its environment.
    + This constraint was explicitly required by the official hardware competition rules [1]–[3].
- C4: The robot shall contain modules that are plug-and-play
adaptable for different IEEE competition requirements.
    + This constraint is applicable to all subsystems of the robot platform in order to make the robot easily adaptable year to year. This in particular applies to the power distribution system by requiring that power connections should be easy to connect and disconnect.
- C7:  The robot shall possess a single emergency stop button
that is accessible and stops all robot movement without removing power to essential processors that is compliant with standard NFPA 79-10 [4].
    + The constraint is required by the IEEE hardware competition rules every year as a safety precaution and is followed by the power distribution system of the robot [1]-[3].
- C8: The robot shall contain a power bus that is not inhibited by DC motor operation.
    + This constraint was made because DC motors can cause interference in the power buses of electronics by supplying a voltage pushing back on their power source, referred to as "back-EMF", inhibiting the function of the power rails for other components. Diode protection is used to prevent this.

### Derived from Broader Implications

- C17: This standard outlines the allowable ampacities of insulated conductors up to 2000 volts. The project will be well under this voltage and is therefore applicable. The standard will need to be followed for the safety of the design team and potential users by ensuring all wire is appropriately rated for the load [5].
    + This constraint is applicable because it outlines the allowable ampacities of insulated conductors up to 2000 Volts. The voltages used in the power distribution system will fall under this limit and so this standard is an applicable constraint of the system.

## Schematic

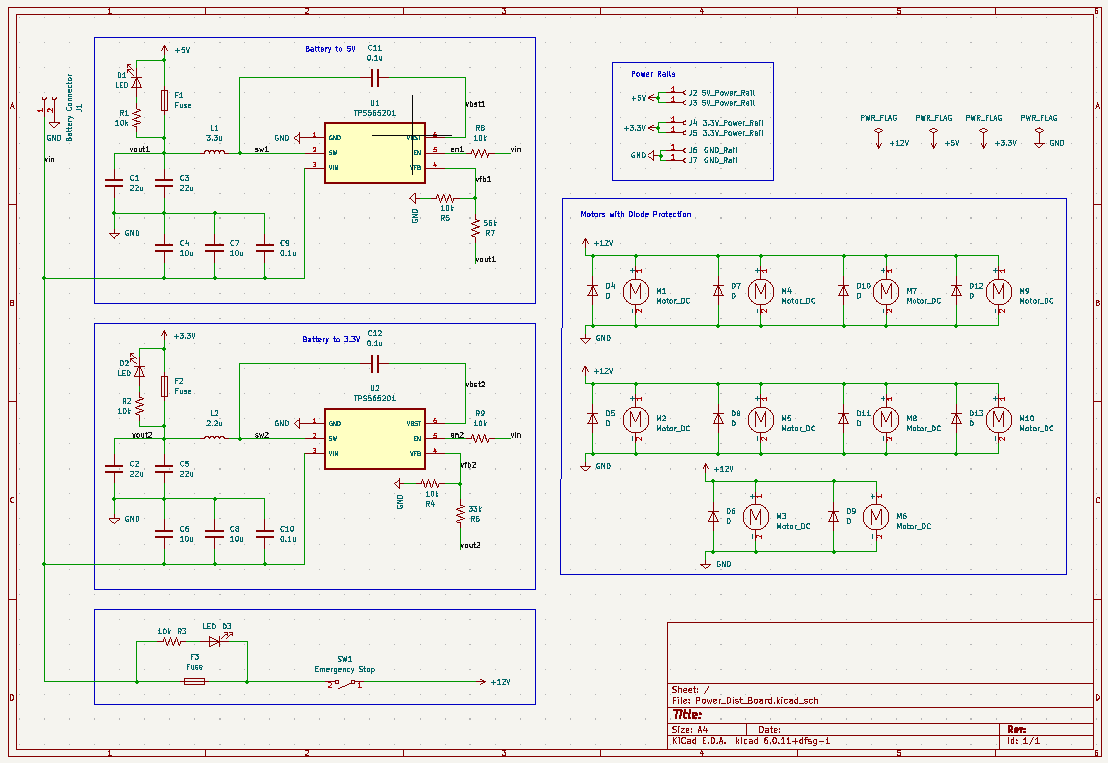
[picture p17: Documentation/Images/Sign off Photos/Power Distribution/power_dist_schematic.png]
Circuit Board Schematic


The schematic for the power distribution circuit board is shown above. The board has a screw terminal connector meant for connecting to the battery. This then supplies the input voltage to the three power rail subcircuits.

The circuit board is based around a single type of buck converter chip, the TPS565201. This chip is a variable voltage regulator buck converter that can source up to 5 A of output current [6]. The output voltage is set by the ratio of feedback resistors connected to the the VFB pin of the chip. The datasheet for the voltage regulator provides a formula for calculating the necessary feedback resistor valuesThe datasheet also provides a table of component values for common output voltages in Table 2. The nearest standard resistor values to the ones provided in this table were the values chosen.

There are two buck converter-based subcircuits on the board, one for the 3.3 V and one for the 5 V rail. The feedback resistors are R5, R7, R4, and R6, which set output voltages of 5 V and 3.3 V, respectively.

The other component values were chosen based on the recommended values given by the manufacturer, Texas Instruments [6]. These values can be found in Table 2 of the datasheet.

There is a 12 V rail specifically designed for supplying power to the motors. Because the motors and their drivers are much less sensitive to slight variations in supply voltage, no voltage regulators are used. Additionally, there are reverse-biased diodes for back-emf protection.

Finally, the circuit design has fuses on each of the power rails to protect the conductors from over-current protection.

## Analysis

Any components references in the analysis below can be found in the table in the section titled "BOM."

### Adequate Power Supply

To ensure that the first constraint is met, that the power distribution system can supply adequate power and current to the other subsystems, the following analysis was done.

The current requirements are a very large constraint of the subsystem. Each component sources its supply voltage directly from the corresponding voltage rail, not through any other component. This is to provide the lowest probability of a cascading failure resulting from chained components. The current requirements of each power rail are shown below.

#### 5 V Rail Current Requirements [7][8][9]
| Item | Part Number | Quantity | Max Current Draw (mA) | Item Current (mA) |
| --- | --- | --- | --- | --- |
| Line Sensor | Pololu QTR-8RC | 1 | 100 | 100 |
| Ultrasonic Distance Sensor | SKU 101020010 | 4 | 8 | 32 |
| Jetson Nano\* | SKU 101020010 | 1 | 2000 | 2000 |
| Total Current |  |  |  | 2132 |

\*The Jetson Nano current requirements depend on the supply method chosen. The Micro-USB connection was chosen in this case.

#### 3.3 V Rail Current Requirements [10][11]
| Item | Part Number | Quantity | Max Current Draw (mA) | Item Current (mA) |
| --- | --- | --- | --- | --- |
| Compass| LIS3MDL | 1 | 0.27 | 0.27 |
| Accelerometer | ADXL345 | 1 | 0.14 | 0.14 |
| Total Current |  |  |  | 0.41 |

#### 12 V Rail Current Requirements [12][13]

| Item | Part Number | Quantity | Max Current Draw (mA) | Item Current (mA) |
| --- | --- | --- | --- | --- |
| Motor | Metal Gearmotor 37Dx73L mm 12V | 4 | 720 | 2880 |
| Motor Driver | L298N Motor Drive Controller Board | 2 | 2000 | 4000 |
| Total Current |  |  |  | 6880 |

The subcircuits for each power rail must be able to supply the required current and more to allow for future expansions. The voltage regulator chips used for the 3.3 V and 5 V rails are the major current limiting factor for those power rails. The datasheet of the TPS565201 buck converter states that the chip can source a nominal output current of 5 A, with a maximum possible output current of 8 A [6]. Using the nominal output current of 5 A, the 3.3 V and 5 V rails can source well over the required current.

The 3.3 V rail can source an additional 1119% (4.59 A) of the current worst-case current draw, and the 5 V rail can source an additional 134% (2.87 A) of the  worst-case current draw from that power rail.

The four images below show the simulated results of the buck-converter subcircuits designed based on the recommended values given in the datasheet of the TPS565201 buck converter chip [6]. The SPICE model used is provided by Texas Instruments on the website for the TPS565201 chip [14].

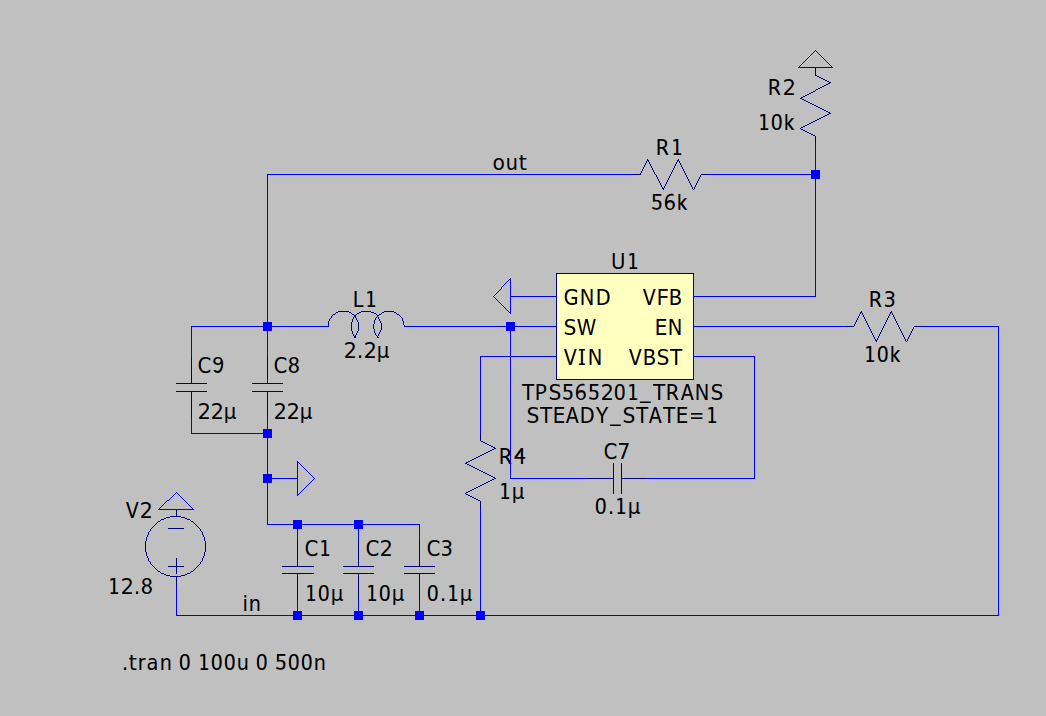
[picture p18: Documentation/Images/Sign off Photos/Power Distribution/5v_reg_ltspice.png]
5V Regulation LTSpice Circuit


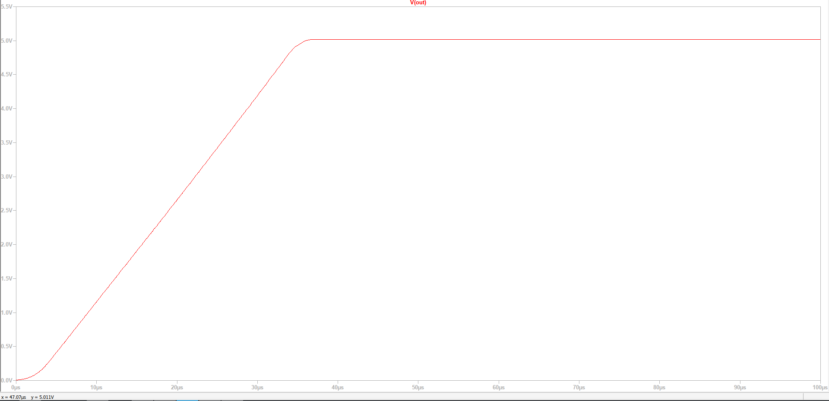
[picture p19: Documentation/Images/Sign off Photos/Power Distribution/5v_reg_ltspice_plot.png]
5V Regulation LTSpice Output Voltage Plot


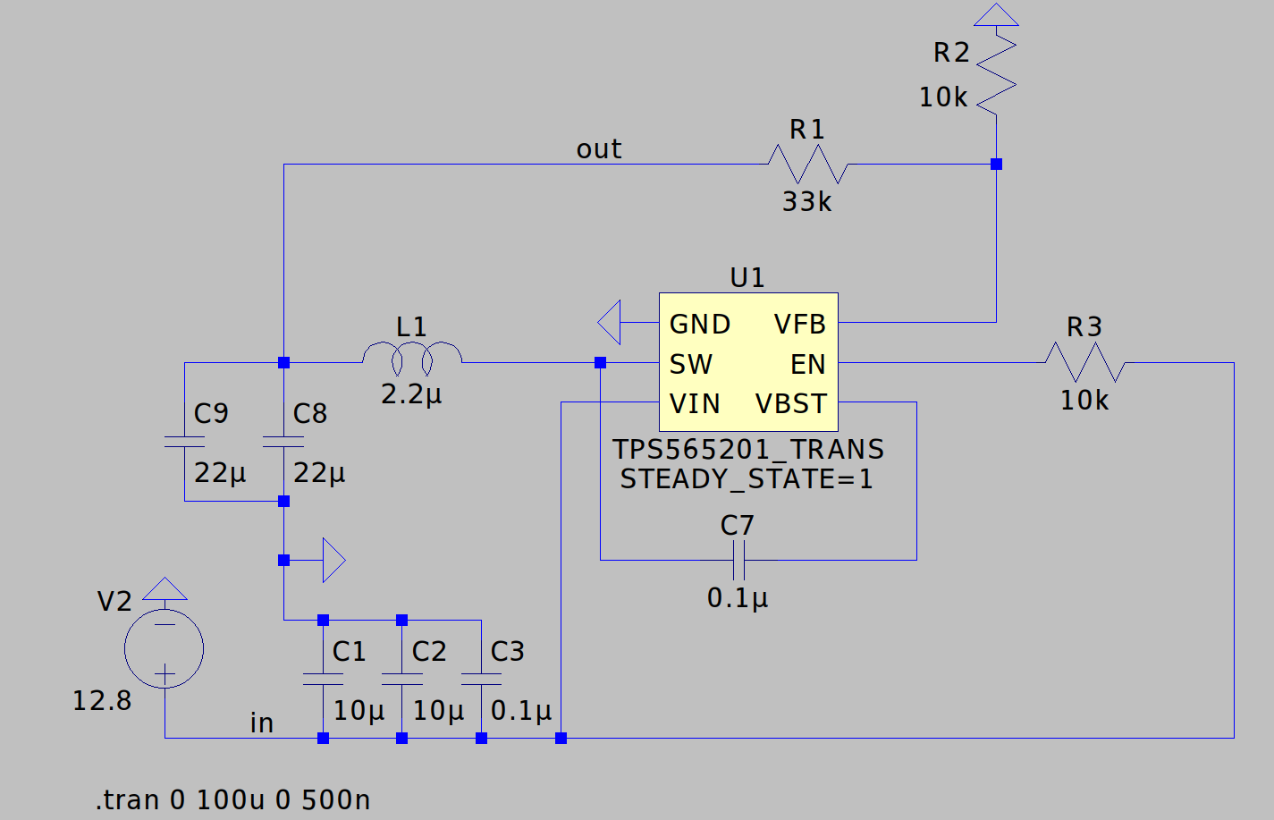
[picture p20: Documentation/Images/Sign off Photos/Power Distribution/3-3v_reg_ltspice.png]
3.3V Regulation LTSpice Circuit


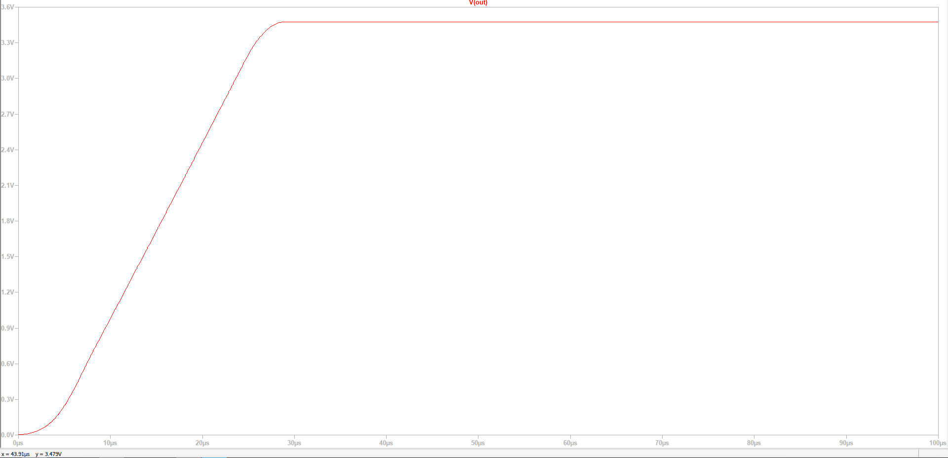
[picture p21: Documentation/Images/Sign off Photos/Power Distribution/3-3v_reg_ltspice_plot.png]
3.3V Regulation LTSpice Output Voltage Plot


As can be seen above, the voltage regulator circuits successfully convert a 12.8 V input voltage, the nominal voltage of the battery chosen, down to 5 V and 3.3 V with minimal start-up delay [15]. The steady-state output voltages calculated by the simulations are 5.011 V and 3.48 V for the 5 V and 3.3 V circuits, respectively. Because the resistor values are chosen based on the values given in the datasheet, the differences between simulated and ideal values are likely just due to inaccuracies in the SPICE model provided. Furthermore, the simulated steady-state values is within the functional tolerance of 3.3 V logic [16].

The datasheet for the TPS565201 states that the chip is able to source 5 A [6]. This means that the 3.3 V and 5 V power rails are both able to source up to 5 A of current. The 12 V rail does not have a voltage regulator, and so it current-limited by the 10 A fuse F3 in the schematic, discussed further later in this document.

The layout of the printed circuit board is shown below. The layout is very heavily based on the recommended layout given in the datasheet of the buck converters and can be found in Figure 30 in the datasheet [6]. The recommended layout was used to ensure the best possible thermal management and current capacity to avoid failures due to overheating or overcurrent.

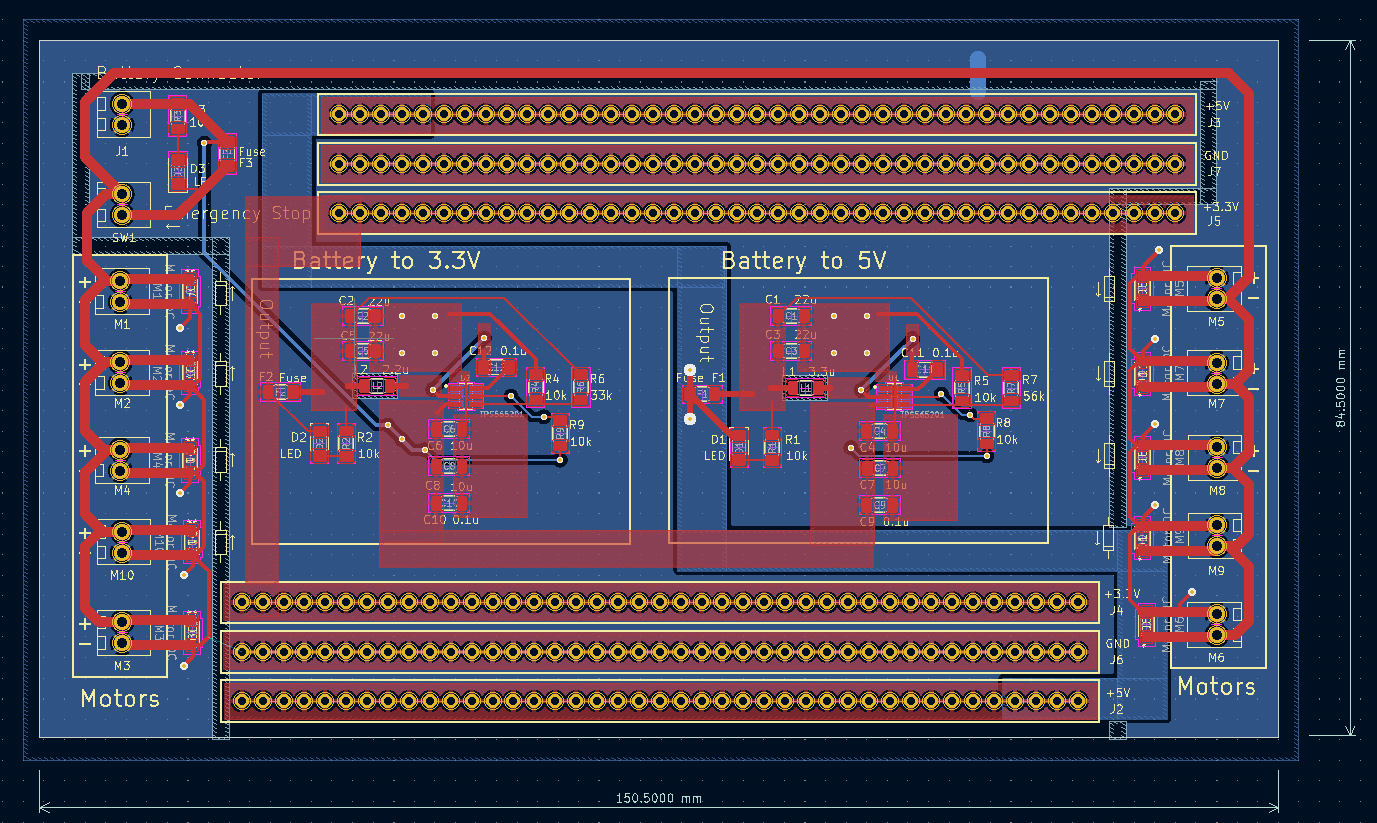
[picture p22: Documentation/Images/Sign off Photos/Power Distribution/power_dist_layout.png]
Power Distribution Printed Circuit Board Layout


The above calculations show that the power distribution system can supply adequate voltages and currents to the components of the robot, satisfying this constraint. A more detailed discussion on the current limits of the different power rails is shown in the section "Allowable Ampacities" below.

### Plug and Play

To ensure that the power distribution system is "plug-and-play," satisfying the second constraint, the power rail connectors were designed such that most standard connectors will be compatible. The through-hole connectors for the 3.3 V, 5 V, and ground rails are spaced apart by 2.54 mm (0.1 in) with a hole diameter of 1 mm. This allows for screw terminals, female pin headers, and any other connectors that have a 2.54 mm connector pitch and connector diameter less than 1 mm to be compatible. There are 82 through hole connectors for each of the three rails mentioned above. This allows for easy power connections that can allow for many components to be quickly connected and unconnected to power depending on the power requirements.

For the 12 V power rails there were less connectors put into place due to less components likely to require a 12 V rail in the future. Additionally, the higher current requirements typical of the 12 V rail require a higher-current connection. The screw terminals used for the motor connections allow for up to 10 A of current, far more than what would be being pulled by the motors used in any non-failure scenario [12][17].

There are still more than enough screw terminals for the base robot, allowing for additional motors and motor drivers to be driven by future designs through the extra screw terminals.

These measures taken for all of the power rails of the robot ensure that the power distribution system of the robot is as plug-and-play and easily adaptable as possible.

### Emergency Stop Button

Another constraint laid out for this subsystem is that there must be an emergency stop button that can be pressed at any time to cease all power supply to the motors but not to the sensors and computational components of the robot. This constraint comes from the IEEE hardware competition rules and the NFPA guidelines on machinery safety precautions [1]-[4].

To accomplish this a screw terminal was placed in series with the 12 V rail. This screw terminal is meant to be connected to a SPST emergency stop button with each end of the SPST switch being connected to each connection on the two-connection screw terminal block, allowing the button to interrupt current to the 12 V rail.

A screw terminal was chosen such that it would allow for adequate current to pass through normally, and could effectively stop current when the button is pressed. The IDEC NWAR-27 emergency stop button was chosen for this. This emergency stop button can adequately handle 10 A of current, and is a normally-closed button that will open the circuit when the button is pressed [18]. Once the button is pressed and the circuit opened, the button must be reset by pulling the button out again.

This emergency stop button will cut all power from the motors when pressed, but leave the sensors and computers on the robot functional, fulfilling this requirement.

### Motor Protection

The next constraint of the power distribution subsystem is that the DC motors cannot interfere with the power rails of the other components. The reason that DC motors interfere with other power rails is that when a motor is switched off it resists the change in current [19]. As it does this, it generates a "back-EMF" that pushes back against the power supply, lowering the supply voltage for all components connected to that rail. To prevent this a diode, called a flyback diode, is inserted in parallel to the motor and is reverse-biased. After this when the motor induces a back-EMF, the induced voltage forces current through the diode, not the power supply, allowing the current to dissipate safely in the diode instead of the power rail.

The circuit board design utilizes reverse-biased diodes across every motor connector. It should be noted that these are optional. If the user does not want the diodes in place or is connecting a motor driver or another component that does not require it, then the circuit design does not require a diode in place. For easy installation, the polarity of the diode is indicated on a drawing next to each of the diodes on the circuit board.

In order to ensure the lowest possible chance of failure, the flyback diodes must be able to sustain the maximum current draw of the motor (about 1 A) and the full reverse-biased source voltage of the motor (about 12 V) [12]. The diodes chosen are able to survive much more than the required current and reverse-bias voltage, and can be found in the datasheet [20].

The diode protection added to the circuit board should provide adequate protection from the worst-case back-EMF resulting from the motor according to the datasheet. This shows that this constraint is also sufficiently met by the design.

Additionally, the motor ground and ground for the rest of the printed circuit board are quasi-isolated to help prevent interference travelling through the ground of the board. This was done by electrically isolating the motor ground plane and normal ground plane except through a small trace connecting the two. This keeps the "grounds" at an equal reference potential, but causes the noise from the motor ground to prefer to not travel to the grounds of the other components.This in addition to the diode protection should prevent the motors from interfering with the DC power buses.

### Allowable Ampacities

The final constraint requires that the circuit board traces fall within the allowable ampacities given by the NFPA standard. The allowable currents, trace widths, and other required values are calculated below using the stated NFPA 79-10 and IPC-2221 standards [4][21].

Aside from the voltage regulator chips, the output 3.3 V rail and 5 V rail currents are limited by the narrowest trace on the output line from the chip. In the case of this board the narrowest trace bottle-necking the output current is the trace immediately connected to the SW pin because it is limited by the space between the chip's pins. All other traces that the output current passes through are wider than this trace and so can support more current. The maximum possible width of the trace connected to the SW pin is 0.5 mm.

The IPC-2221 standard gives formulas and data to calculate the maximum current of this trace [21]. From Figure A and Figure B in Appendix B, the maximum current can be calculated based on the maximum required change in temperature. The maximum acceptable change in temperature can be found by looking at the transition temperature of the PCB laminate material FR4, the temperature at which the laminate will begin to degrade, and is around 110 degrees Celsius [21]. Because the transition temperature of FR4 is so much lower than the melting point of copper (1083 Celsius), the FR4 transition temperature is the upper bound on trace temperature limiting the current through the trace [23].

To find the maximum current of the trace, the trace cross section needs to be found, which requires the width and thickness of the trace. The width is limited to 0.5 mm. Thickness of PCB copper traces is often given in oz/ft^2, which is the thickness of that weight of copper if it were rolled into a square-foot area [24]. To allow for higher current, 2 oz/ft^2 was chosen instead of the default option of 1 oz/ft^2. Using Figure B of Appendix B of the IPC-2221 standard after converting the trace width to inches, the cross section of the trace is found to be about 50 square-mils.

To then find the maximum allowable current, Figure A is used [21]. Assuming that the trace begins at a room temperature of 25 Celsius and that the maximum allowable temperature is 110 Celsius, this yields a maximum change in temperature of 85 degrees Celsius. Using the graph, this yields a maximum current a little over 6 Amps. For more precise calculations, the FR4 source referenced earlier provides the formula for calculating maximum current in equation (1) [22]. When the aforementioned values are used in this formula, a maximum current of 6.28 A is calculated.

Because this current limit is higher than the output current limit of the voltage regulator chips, the trace will not fail within the normal operating parameters of the voltage regulators. To further prevent failures from occurring in the case of a sudden increase in current, a 6 A fuse is placed on the 3.3 V and 5 V rails near the output from the chip so that the fuse will blow before the trace can sustain any damage from overcurrent.

A similar method is used for calculating the maximum supportable current of the 12 V rail. The narrowest trace of the 12 V rail is 1.25 mm wide. Using Figure B from Appendix B in the IPC-2221 standard document after converting the width to inches, the cross section in square-mils is about 125 square-mils [21]. Using the same formula given in the FR4 source document, the maximum current given an 85 degree Celsius change in temperature from room temperature is about 11.7 A [22]. To prevent damage to the conductor, a 10 A fuse is inserted at the beginning of the 12 V rail so that the fuse will blow before the 12 V rail trace can sustain damage.

Finally, the screw terminals used for connecting the motors to the 12 V power rail can supply up to 10 A safely [17]. This indicates that all parts of the 12 V power supply can support the high amounts of current that may be required of it.

The above calculations ensure that the components and traces used on the printed circuit board are within the acceptable value range. This shows that the fifth and final constraint is met by this design.

### Start Button

A button or switch of some kind that is able to be used for the starting of the robot is also required. This button will be connected to the 5 V power rail and to one of the digital input pins on the Jetson Nano. 

When this switch is flipped, the Jetson Nano will detect that the digital input pin is high and begin navigating the environment, satisfying this requirement. A switch was chosen for this that can sustain much more than the required voltage and current [25].

## BOM

| Item | Part Number | Quantity | Price/Unit | Item Price |
| --- | --- | --- | --- | --- |
| Buck Converter 	| TPS565201 	| 10 | $1.292 | $12.92 |
| Flyback Diode 	| RB070MM 	| 20 | $0.277 | $5.54  |
| LED 	| QBLP615 	| 20 | $0.289 | $5.78  |
| 6 Amp Fuse 	| QBLP615 	| 10 | $0.700 | $7.00  |
| 10 Amp Fuse 	| QBLP615 	| 10 | $0.312 | $3.12  |
| Screw Terminal 	| 0397730002  	| 25 | $1.2388  | $30.97 |
| Female Headers 	| 5583 	| 5  | $0.95	| $4.75  |
| Emergency Stop Button | NWAR-27 	| 2  | $5.70	| $11.40 |
| On/Off Switch | ST141D00 	| 1  | $6.07	| $6.07  |
| Printed Circuit Board | 	| 5  | $5.16	| $25.80 |
| 10 kOhm Resistor  	| RMCF1206FT10K0  | 50 | $0.0146  | $0.73  |
| 33 kOhm Resistor  	| RMCF1206JT33K0  | 20 | $0.0200  | $0.40  |
| 56 kOhm Resistor  	| RMCF1206JT56K0  | 20 | $0.0200  | $0.40  |
| 0.1 uFarad Capacitor  | CL31B104KBCNNNC | 30 | $0.07800 | $2.34  |
| 10 uFarad Capacitor | CL31A106KAHNNNE | 30 | $0.122 | $3.66  |
| 22 uFarad Capacitor | CL31A226KAHNNNE | 30 | $0.239 | $7.17  |
| 2.2 uHenry Inductor | SPM6530T-2R2M | 10 | $0.991 | $9.91 |
| 3.3 uHenry Inductor | SPM6530T-3R3M | 10 | $0.991 | $9.91  |
| Total 	| 	|	| 	| $100.26 |

The component quantities were chosen to provide enough for several full printed circuit boards to be constructed. For example, two buck converters are required per board which requires ten total buck converters for five full PCBs to be constructed. Five PCBs was chosen as it is the minimum quantity offered by JLCPCB, a commonly used PCB manufacturer.

## References

[1] “IEEE SOUTHEASTCON 2024 STUDENT HARDWARE COMPETITION RULES Version 5.6,” Sep. 2023. [Online]. Available: https://ieeesoutheastcon.org/wp-content/uploads/sites/497/SEC24-HW-Competition V5.6-1.pdf

[2] “IEEE SoutheastCon 2023 Hardware Competition Rules,”
Oct. 2022. [Online]. Available: https://github.com/lchapman42/Control-Sensing-Wireless-Charging-Robot/blob/main/Documentation/Background%20DocumentsIEEE%20SoutheastCon%202023%20Hardware%20Competiti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

[3] “IEEE SoutheastCon 2022 Hardware Competition Rules,”
Mar. 2021. [Online]. Available: https://github.com/lchapman42/Control-Sensing-Wireless-Charging-Robot/tree/main/Documentation

[4] “NFPA 79: Electrical Standard for Industrial Machinery.” [Online]. Available: https://link.nfpa.org/free-access/publications/79/2021

[5] “Using the National Electrical Code® (NEC ®) Ampacity Charts,” May
2021. [Online]. Available: https://www.nfpa.org/∼/media/Files/Code%
20or%20topic%20fact%20sheets/NECAmpacityWorkflow.pdf

[6] “TPS565201 4.5-V to 17-V Input, 5-A Synchronous Step-Down Voltage Regulator.” Texas Instruments, Sep. 2017. Accessed: Oct. 13, 2023. [Online]. Available: https://www.ti.com/lit/ds/symlink/tps565201.pdf?ts=1698731666929

[7] “Pololu - QTR-8RC Reflectance Sensor Array.” Accessed: Oct. 22, 2023. [Online]. Available: https://www.pololu.com/product/961

[8] “Grove - Ultrasonic Distance Sensor.” Accessed: Oct. 20, 2023. [Online]. Available: https://www.seeedstudio.com/Grove-Ultrasonic-Distance-Sensor.html

[9] “Jetson Nano Datasheet.” Nvidia, 2014. Accessed: Oct. 18, 2023. [Online]. Available: https://developer.download.nvidia.com/assets/embedded/secure/jetson/Nano/docs/JetsonNano_DataSheet_DS09366001v1.1.pdf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

[10] “LIS3MDL - Digital output magnetic sensor : ultra-low-power, high-performance 3-axis magnetometer - STMicroelectronics.” STMicroelectronics, May 2017. Accessed: Oct. 20, 2023. [Online]. Available: https://www.st.com/en/mems-and-sensors/lis3mdl.html

[11] “ADXL345 Datasheet and Product Info | Analog Devices.” Analog Devices. Accessed: Oct. 16, 2023. [Online]. Available: https://www.analog.com/en/products/adxl345.html

[12] “Pololu - 150:1 Metal Gearmotor 37Dx73L mm 12V with 64 CPR Encoder (Helical Pinion),” Polulu. Accessed: Oct. 16, 2023. [Online]. Available: https://www.pololu.com/product/2828/specs

[13] “Dual full-bridge driver.” STMicroelectronics. [Online]. Available: https://www.sparkfun.com/datasheets/Robotics/L298_H_Bridge.pdf

[14] “TPS565201 data sheet, product information and support | TI.com,” Texas Instruments. Accessed: Oct. 10, 2023. [Online]. Available: https://www.ti.com/product/TPS565201

[15] “LIS3MDL - Digital output magnetic sensor : ultra-low-power, high-performance 3-axis magnetometer - STMicroelectronics.” STMicroelectronics, May 2017. Accessed: Oct. 22, 2023. [Online]. Available: https://www.st.com/en/mems-and-sensors/lis3mdl.html

[16] “Low Voltage Logic Interfacing.” [Online]. Available: https://www.analog.com/media/en/training-seminars/tutorials/MT-098.pdf

[17] “397730002.” Molex. Accessed: Oct. 24, 2023. [Online]. Available: https://tools.molex.com/pdm_docs/sd/397730002_sd.pdf

[18] “TW Series — 22mm NEMA Style Pushbuttons.” IDEC. Accessed: Oct. 23, 2023. [Online]. Available: https://www.mouser.com/datasheet/2/650/idec_TWSeries-1894031.pdf

[19] G. Recktenwald, “Basic DC Motor Circuits.” Portland State University. Accessed: Oct. 18, 2023. [Online]. Available: http://web.cecs.pdx.edu/~eas199/A/topics/dc_motor/DC_motor_circuits_slides.pdf

[20] “RB070MM-30 Schottky Barrier Diode.” ROHM Semiconductor, 2017. Accessed: Oct. 16, 2023. [Online]. Available: https://fscdn.rohm.com/en/products/databook/datasheet/discrete/diode/schottky_barrier/rb070mm-30tr-e.pdf

[21] “IPC-2221A Generic Standard on Printed Board Design.” IPC, May 2003. [Online]. Available: https://www-eng.lbl.gov/~shuman/NEXT/CURRENT_DESIGN/TP/MATERIALS/IPC-2221A(L).pdf

[22] J. Adam, “New correlations between electrical current and temperature rise in PCB traces,” in Twentieth Annual IEEE Semiconductor Thermal Measurement and Management Symposium (IEEE Cat. No.04CH37545), San Jose, CA, USA: IEEE, 2004, pp. 292–299. doi: 10.1109/STHERM.2004.1291337.

[23] “nglos324 - copper,” Princeton. Accessed: Oct. 13, 2023. [Online]. Available: https://www.princeton.edu/~maelabs/mae324/glos324/copper.htm

[24] “Fabricating Boards,” MIT. Accessed: Oct. 19, 2023. [Online]. Available: https://pcb.mit.edu/lectures/board_fab/

[25] “ST1 Series Toggle Switch.” E-Switch. Accessed: Nov. 14, 2023. [Online]. Available: https://sten-eswitch-13110800-production.s3.amazonaws.com/system/asset/product_line/data_sheet/136/ST1.pdf

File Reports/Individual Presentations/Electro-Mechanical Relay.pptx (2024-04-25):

## Electro-Mechanical Relay

By: Mabel Olson

## Overview

- What is an electro-mechanical relay?
- What are the components?
- How does it operate?
- What is the theory behind the operation?
- What are the types?
- What is the application?

## Electro-Mechanical Relay

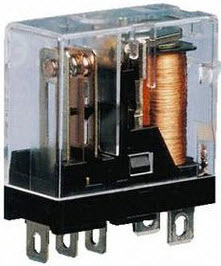
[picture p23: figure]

- An electromechanical relay is essentially a switch that converts electric energy to mechanical energy to either connect or disconnect another circuit depending on the type of relay.

## Components

1. Coil
2. Armature
3. Spring
4. Contacts

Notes: Coil – The coil is an inductor or a length of wire that is wrapped around a magnetic core. When a current is passed through it a magnetic field is produced.
Spring - The holds the armature in a specific initial condition and returns it to that position once the relay is disengaged.
Armature - The armature is the mechanical component of a relay that moves to either engage or disengage the relay. This component is moved by the magnetic field produced by the coil.
Contacts - The contacts are what the armature end moves between to determine the state of the relay.

## Components

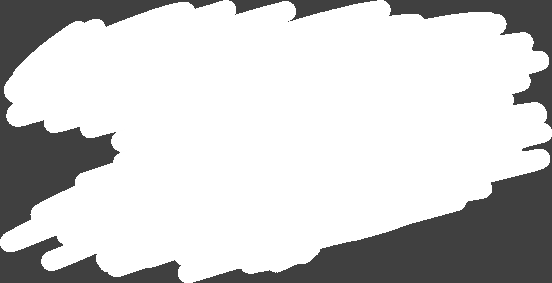
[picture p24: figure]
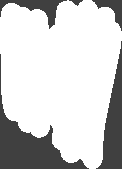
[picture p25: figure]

1. Coil
2. Armature
3. Spring
4. Contacts

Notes: Coil – The coil is an inductor or a length of wire that is wrapped around a magnetic core. When a current is passed through it a magnetic field is produced.
Spring - The holds the armature in a specific initial condition and returns it to that position once the relay is disengaged.
Armature - The armature is the mechanical component of a relay that moves to either engage or disengage the relay. This component is moved by the magnetic field produced by the coil.
Contacts - The contacts are what the armature end moves between to determine the state of the relay.

## Components


1. Coil
2. Armature
3. Spring
4. Contacts

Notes: Coil – The coil is an inductor or a length of wire that is wrapped around a magnetic core. When a current is passed through it a magnetic field is produced.
Spring - The holds the armature in a specific initial condition and returns it to that position once the relay is disengaged.
Armature - The armature is the mechanical component of a relay that moves to either engage or disengage the relay. This component is moved by the magnetic field produced by the coil.
Contacts - The contacts are what the armature end moves between to determine the state of the relay.

## Components


1. Coil
2. Armature
3. Spring
4. Contacts

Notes: Coil – The coil is an electromagnet. When a current is passed through it a magnetic field is produced.
Armature - The armature is the mechanical component of a relay that moves to either engage or disengage the relay. This component is moved by the magnetic field produced by the coil.
Spring - The holds the armature in a specific initial condition and returns it to that position once the relay is disengaged.
Contacts - The contacts are what the armature end moves between to determine the state of the relay.

## Components

1. Coil
2. Armature
3. Spring
4. Contacts

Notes: Coil – The coil is an inductor or a length of wire that is wrapped around a magnetic core. When a current is passed through it a magnetic field is produced.
Spring - The holds the armature in a specific initial condition and returns it to that position once the relay is disengaged.
Armature - The armature is the metal, mechanical component of a relay that moves to either engage or disengage the relay. This component is moved by the magnetic field produced by the coil.
Contacts - The contacts are what the armature end moves between to determine the state of the relay.

## Operation – 3 Stages

1. Activation – During the activation stage, an electric current from the control circuit is sent through the coil. The current within the coil produces a magnetic field. This magnetic field attracts the metal armature of the relay towards the coil.
2. Movement – The movement of the armature either completes or disconnects the main circuit(s) via the contacts depending on the type of relay.
3. Deactivation – Once the control circuit is deactivated, the coil is no longer producing a magnetic field. As a result, the armature moves back to its initial position.

## Coil – What is a Magnetic Field?

- When a current flows through the coil from the control circuit a magnetic field is produced
- The distribution of magnetic force
  - Strength is determined by the number of coils and/or the magnitude of the current
  - The direction of current determines the direction of the magnetic field
    - Right-hand grip rule
- B= (μ_0 I)/(2πr)= μ_0 Nl

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

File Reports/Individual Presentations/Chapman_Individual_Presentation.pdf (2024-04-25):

# Microstrip Antennas

## Luke Chapman

# What is a Microstrip Antenna?


- Patch antennas consist of a thin metallic strip above a ground plane separated by a dielectric substrate
- Microstrip (patch) antennas are used extensively in applications where physical dimensions are limited
- Radiation is caused by an electric field induced between the patch and the ground plane
- The primary direction of radiation is normal to the plane of the patch
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

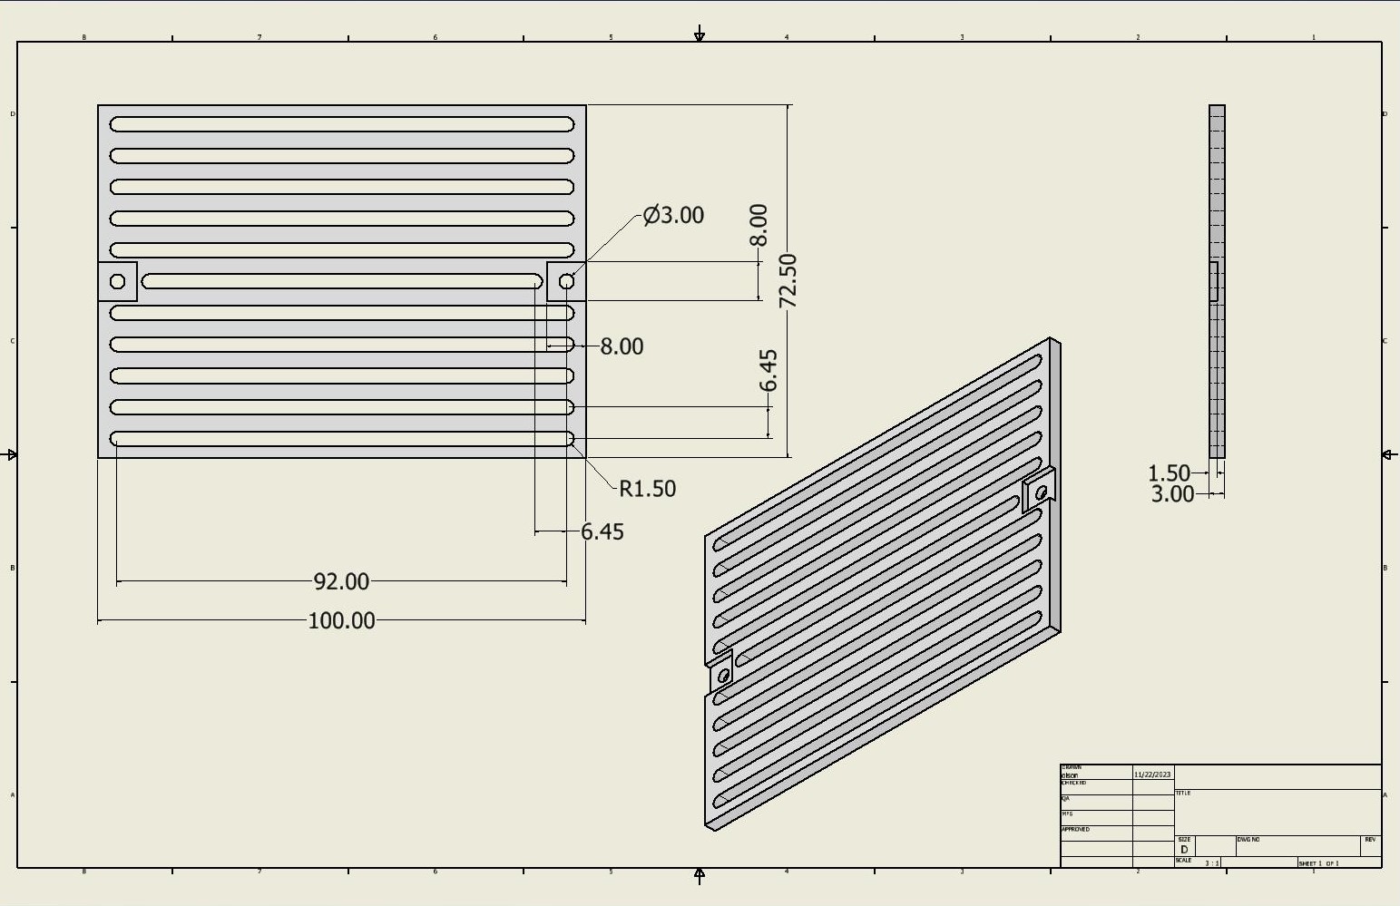
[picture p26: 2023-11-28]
Documentation/Images/Sign off Photos/Layout Organization/Slotted Peice Middle Schematic.jpg

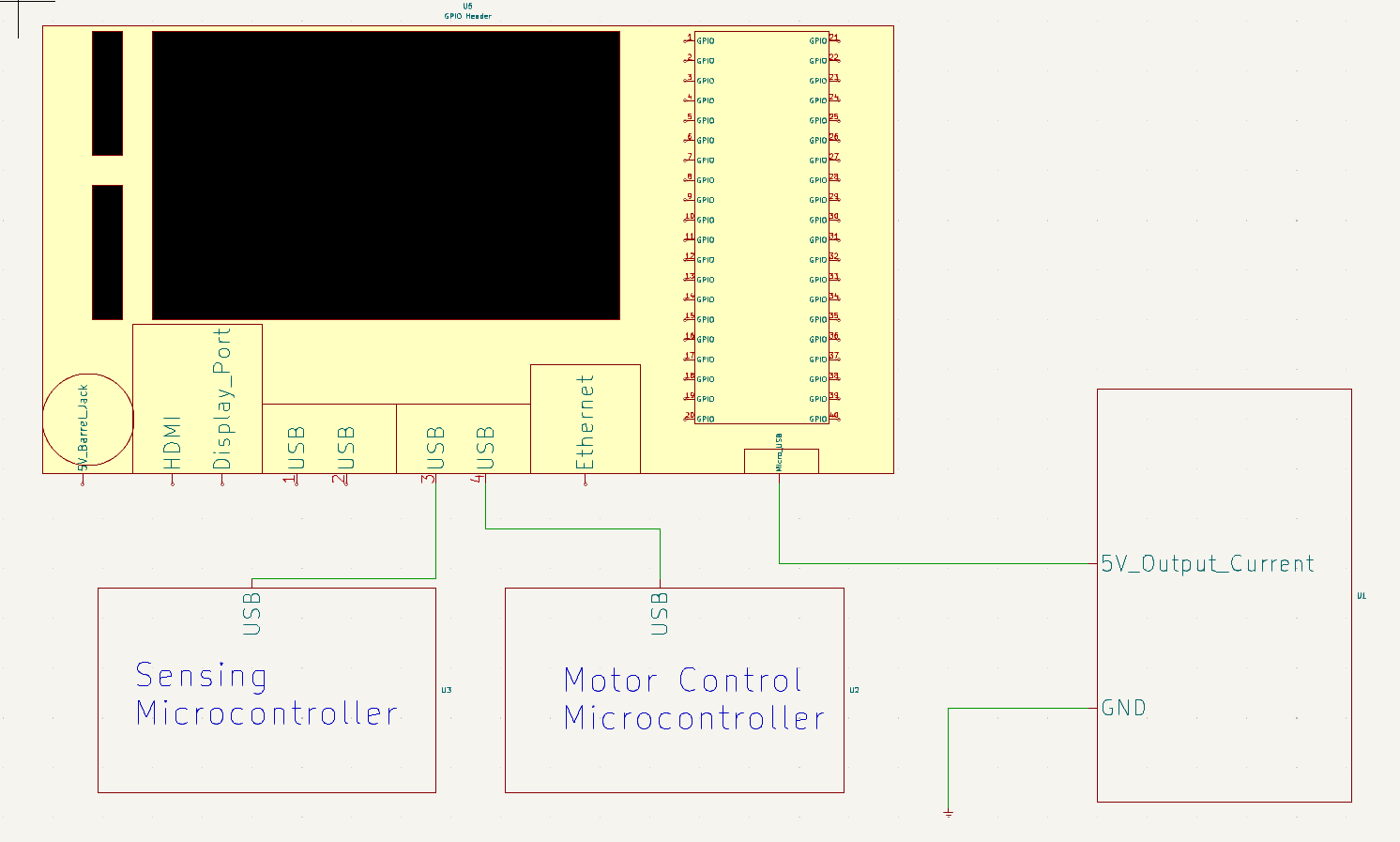
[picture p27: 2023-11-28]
Documentation/Images/Sign off Photos/Master Control/Master_Control_Pinout.png

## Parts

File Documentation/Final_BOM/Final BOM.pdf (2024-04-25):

Component | Description | Subsystem | Part Number | Manufacturer | Quantity | Price Per Unit | Total Cost
2-56 Hex Nut (25 pk) | Connects line sensor to attachment | Attachments | 1067 | Polulu | 1 | $2.25 | $2.25
2-56 Screw (25 pk) | Connects line sensor to attachment | Attachments | 2715 | Polulu | 1 | $1.39 | $1.39
6 mm T Slot Nuts (100 pk) | Allows for attachments to extruded aluminum | Attachments | N/A | Amazon | 1 | $9.78 | $9.78
Assorted Nylon Hardware | Assorted hardware for attaching components | Attachments | N/A | Amazon | 1 | $7.99 | $7.99
PLA Filment | For 3D printing components | Attachments | N/A | Amazon | 1 | $17.99 | $17.99
1/4 - 20 Screw (20 pk) | Hardware for line following sensor attachment | Attachments | N/A | Amazon | 1 | $8.99 | $8.99
1/4 Washer (100 pk) | Hardware for line following sensor attachment | Attachments | N/A | Amazon | 1 | $6.19 | $6.19
M4 - 8 mm Screws (50 pk) | Screws for T-slot nuts | Attachments | N/A | Amazon | 1 | $7.99 | $7.99
Panel Mount 3-Prong Receptacle | Female IEC 320 C13 | Battery Management | 6100.33 | SCHURTER Inc. | 5 | $1.15 | $5.75
IEC 320 C13 - C14 Power Cable | IEC 3-Prong power cable for connecting battery charger to receptacle | Battery Management | AK500-OE-11-.5 | Assmann WSW Components | 1 | $3.67 | $3.67
C13 - C13 Adapter | IEC Female-Female adapter for connecting cable to receptacle | Battery Management | C13 to C13 Power adapter | TeKit | 1 | $14.99 | $14.99
12 Foot 3-Prong AC Power Cable | IEC-NEMA 3-Prong power cable for connecting to standard US wall socket | Battery Management | P010-012 | Tripp Lite | 2 | $10.62 | $21.24
Lithium Iron Phosphate Battery Charger | Lithium Iron Phosphate battery charger that will charge and manage battery | Battery Management | PCCG-LFP14.4V10A | ZEUS Battery Products | 1 | $129.27 | $129.27

Lithium Iron Phosphate Battery | 12.8 V 7.2 Ah lithium iron phosphate battery that serves as the main power source for the robot | Battery Management | PSL-SC-1270 F2 | Power Sonic Corporation | 1 | $91.43 | $91.43
6 mm Aluminum Corner Connectors (20 pk) | Connects extruded aluminum together | Chassis Frame | N/A | Amazon | 1 | $13.64 | $13.64
300 mm Extruded Aluminum (4 pk) | The horizontal bars of chassis frame | Chassis Frame | N/A | Amazon | 1 | $17.99 | $17.99
250 mm Extruded Aluminum (4 pk) | The vertical bars of chassis frame | Chassis Frame | N/A | Amazon | 1 | $16.99 | $16.99
M3 - 8 mm Flat Screws (50 pk) | Flat screws from slotted peices to attach without raised heads | Layout and Organization | N/A | Amazon | 1 | $6.49 | $6.49
Wire Labels | Labels for wire organization | Layout and Organization | N/A | Amazon | 1 | $9.00 | $9.00
M3 Nut (50 pk) | Nuts for flat screws | Layout and Organization | N/A | Amazon | 1 | $4.34 | $4.34
Spacer Stand off Screws | Spacers for microcontrollers | Layout and Organization | N/A | Amazon | 1 | $13.99 | $13.99
Reflectance Array | Line following sensor | Line Sensing | 961 | Pololu | 1 | $9.95 | $9.95
Grove - Ultrasonic Distance Sensor V2.0 | Ultrasonic transducer that utilizes ultrasonic waves to measure distance. | Location Sensing | 101020010 | Seeed Technology Co., Ltd | 4 | $4.30 | $17.20
Jetson Nano | Master Controller for mapping, localization, and communication | Master Control | N/A | NVIDIA | 1 | $149.00 | $149.00
Keyboard and Mouse | Used for interfacing with Jetson Nano | Master Control | N/A | HP | 1 | $15.99 | $15.99
Memory Card | Memory for Jetson Nano | Master Control | N/A | SanDisk | 1 | $26.50 | $26.50
MicroUSB cable | Power Cable for Jetson Nano | Master Control | N/A | StarTech | 1 | $4.95 | $4.95
Motor Mounts (2- pack) | Connects motor to the chassis | Motor Control | 2676 | Pololu | 2 | $9.95 | $19.90
Motor with Encoder | Moves robot and sends info through encoder | Motor Control | 2828 | Pololu | 4 | $51.95 | $207.80

Mecanum Wheels (4-pack) | Wheels for 360 motion | Motor Control | 14209 | Orzorobotics | 1 | $17.00 | $17.00
Aluminum Mounting Hub | Aluminum hub that connects the wheels to the motor and has a 6mm opening | Motor Control | 18077 | Orzorobotics | 4 | $6.90 | $27.60
Motor Driver (4- pack) | Driver to control motors based on microcontroller input | Motor Control | L298N | HiLetgo | 1 | $2.87 | $2.87
Microcontroller (Arduino Mega) | Microcontroller | Motor Control | Megaa 2560 Rev3 | Arduino | 1 | $43.56 | $43.56
Grove I2C Bus | I2C Bus | Navigation Microcontroller | N/A | Seed Studio | 4 | $1.70 | $6.80
OLED Display | I2C Display | Navigation Microcontroller | N/A | Amazon | 1 | $8.95 | $8.95
Arduino Mega | Microcontroller | Navigation Microcontroller | N/A | Amazon | 1 | $43.56 | $43.56
ESP 32 | Wifi Module | Navigation Microcontroller | N/A | Amazon | 1 | $19.95 | $19.95
Grove - Time of Flight Distance Sensor | High speed, high accuracy and long-range ToF distance sensor based on VL53L0X. | Object Detection Sensing | 101020532 | Seeed Technology Co., Ltd | 8 | $36.99 | $295.92
Accelerometer | Sensor to detect heading | Orientation | 4517 | Adafruit Industries LLC | 1 | $19.95 | $19.95
Grove Connectors | I2C bus for sensors | Orientation | 4528 | Adafruit Industries LLC | 1 | $1.95 | $1.95
Male/Female Pin Headers | 3.54 mm pitch female pin headers for 3.3 V and 5 V rail connections | Power Distribution | 5583 | Adafruit Industries LLC | 5 | $0.95 | $4.75
Screw Terminals | 2.54 mm pitch screw terminals for 3.3 V and 5 V rail connections | Power Distribution | 397730002 | Molex | 25 | $1.24 | $30.97
10 A Fuse | 12 V rail protection fuse | Power Distribution | 0685H9100-01 | Bel Fuse Inc. | 10 | $0.31 | $3.12
6 A Fuse | 3.3 V and 5 V rail protection fuse | Power Distribution | 0685P6000-01 | Bel Fuse Inc. | 10 | $0.70 | $7.00
10 uFarad Capacitor | 10 uFarad 1206 surface mount capacitor | Power Distribution | CL31A106KAHNNN E | Samsung Electro-Mechanics | 30 | $0.12 | $3.66
22 uFarad Capacitor | 22 uFarad 1206 surface mount capacitor | Power Distribution | CL31A226KAHNNN E | Samsung Electro-Mechanics | 30 | $0.24 | $7.17

0.1 uFarad Capacitor | 0.1 uFarad 1206 surface mount capacitor | Power Distribution | CL31B104KBCNNN C | Samsung Electro-Mechanics | 30 | $0.08 | $2.34
Printed Circuit Board | Power distribution printed circuit board that takes power from battery and supplies power to 3.3 V, 5 V, and 12 V rails | Power Distribution | N/A | JLCPCB | 5 | $5.16 | $25.80
Emergency Stop Button | Push and reset emergency stop button for cutting power to motors | Power Distribution | TWTADE / 22mm 2 NC Red Mushroom Latching Emergency Stop Push Button Switch 10A 600V YW1B-V4E02R | TWTADE | 2 | $12.99 | $25.98
LED | Light emitting diode for fuse blowing indicator | Power Distribution | QBLP615 | QT Brightek (QTB) | 20 | $0.29 | $5.78
Flyback Diode | Schottky Diode for back-EMF motor protection | Power Distribution | RB070MM | Rohm Semiconductor | 20 | $0.28 | $5.54
10k Ohm Resistor | 10 kOhm 1206 surface mount resistor | Power Distribution | RMCF1206FT10K0 | Stackpole Electronics Inc | 50 | $0.01 | $0.73
33k Ohm Resistor | 33 kOhm 1206 surface mount resistor | Power Distribution | RMCF1206JT33K0 | Stackpole Electronics Inc | 20 | $0.02 | $0.40
56k Ohm Resistor | 56 kOhm 1206 surface mount resistor | Power Distribution | RMCF1206JT56K0 | Stackpole Electronics Inc | 20 | $0.02 | $0.40
2.2 uH Inductor | 2.2 uHenry surface mount inductor | Power Distribution | SPM6530T-2R2M | TDK Corporation | 10 | $0.99 | $9.91
3.3 uH Inductor | 3.3 uHenry surface mount inductor | Power Distribution | SPM6530T-3R3M | TDK Corporation | 10 | $0.99 | $9.91
On/Off Switch | SPST Toggle switch for starting robot | Power Distribution | ST141D00 | E-Switch | 1 | $6.07 | $6.07
3.3/5V Regulator | High Current Reconfigurable Buck Converter | Power Distribution | TPS565201 | Texas Instruments | 10 | $1.29 | $12.92
Aluminum Foil | Aluminum foil for capacitive wireless power transfer sheets | Wireless Charging | Amazon Basics Aluminum Foil, 250 Sq Ft | Amazon | 1 | $13.49 | $13.49

Magnet Wire | Magnet wire for transformer and quarter-wave resonators for capacitive wireless power transfer | Wireless Charging | 610222 | CNC Tech | 1 | $120.57 | $120.57
Total without Wireless Charing | | | | | 58 | | $1,513.21
Total | | | | | 60 | | $1,647.27

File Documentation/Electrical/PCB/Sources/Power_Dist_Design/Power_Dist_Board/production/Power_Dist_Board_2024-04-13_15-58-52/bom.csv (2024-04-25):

Designator | Footprint | Quantity | Value | LCSC Part #
C1, C2, C3, C5 | 1206 | 4 | 22u
C10, C11, C12, C13, C14, C15, C16, C17, C18, C20, C21, C22, C9 | 1206 | 13 | 0.1u
C19 | 1206 | 1 | C
C4, C6, C7, C8 | 1206 | 4 | 10u
D1, D2, D3 | 1206 | 3 | LED
F1, F2, F3 | 1206 | 3 | Fuse
J1 | Molex_Screw_Term_0397730002 | 1 | Battery Connector
J10 | GND_Bridge | 1 | GND_Bridge_3
J2, J3 | Pwr_Rail_Conn_Custom | 2 | +5V
J4, J5 | Pwr_Rail_Conn_Custom | 2 | +3.3V
J6, J7 | Pwr_Rail_Conn_Custom | 2 | GND
J8 | GND_Bridge | 1 | GND_Bridge_1
J9 | GND_Bridge | 1 | GND_Bridge_2
L1 | IND_SPM6530_TDK | 1 | 3.3u
L2 | IND_SPM6530_TDK | 1 | 2.2u
M1, M10, M2, M3, M4, M5, M6, M7, M8, M9 | Molex_Screw_Term_0397730002 | 10 | Motor_DC
R1, R2, R3, R4, R5, R8, R9 | 1206 | 7 | 10k
R6 | 1206 | 1 | 33k
R7 | 1206 | 1 | 56k
SW1 | Molex_Screw_Term_0397730002 | 1 | Emergency Stop
U1, U2 | TPS565201 | 2 | TPS565201

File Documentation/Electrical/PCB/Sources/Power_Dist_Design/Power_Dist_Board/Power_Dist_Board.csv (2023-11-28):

Id | Designator | Footprint | Quantity | Designation | Supplier and ref
1 | J9 | GND_Bridge | 1 | GND Bridge 2
2 | D12,D5,D4,D13,D9,D7,D8,D6,D10,D11 | DIO_RB051MM_ROM-M | 10 | D
3 | M3,M7,M2,M8,M9,M6,M1,M5,M10,M4 | Molex_Screw_Term_0397730002 | 10 | Motor_DC
4 | C8,C4,C6,C7 | C_1206_3216Metric_Pad1.33x1.80mm_HandSolder | 4 | 10u
5 | J8 | GND_Bridge | 1 | GND Bridge 1
6 | J5,J4 | Pwr_Rail_Conn_Custom | 2 | 3.3V_Power_Rail
7 | C3,C1,C5,C2 | C_1206_3216Metric_Pad1.33x1.80mm_HandSolder | 4 | 22u
8 | L1 | R_1206_3216Metric_Pad1.30x1.75mm_HandSolder | 1 | 3.3u
9 | D3,D1,D2 | LED_1206_3216Metric_Pad1.42x1.75mm_HandSolder | 3 | LED
10 | R1,R5,R2,R4,R9,R3,R8 | R_1206_3216Metric_Pad1.30x1.75mm_HandSolder | 7 | 10k
11 | C9,C12,C10,C11 | C_1206_3216Metric_Pad1.33x1.80mm_HandSolder | 4 | 0.1u
12 | L2 | R_1206_3216Metric_Pad1.30x1.75mm_HandSolder | 1 | 2.2u
13 | J7,J6 | Pwr_Rail_Conn_Custom | 2 | GND_Rail
14 | F2,F1,F3 | Fuse_1206_3216Metric_Pad1.42x1.75mm_HandSolder | 3 | Fuse
15 | U1,U2 | TPS565201 | 2 | TPS565201
16 | J1 | Molex_Screw_Term_0397730002 | 1 | Battery Connector
17 | J3,J2 | Pwr_Rail_Conn_Custom | 2 | 5V_Power_Rail
18 | R7 | R_1206_3216Metric_Pad1.30x1.75mm_HandSolder | 1 | 56k
19 | J10 | GND_Bridge | 1 | GND_Bridge_3
20 | SW1 | Molex_Screw_Term_0397730002 | 1 | Emergency Stop
21 | R6 | R_1206_3216Metric_Pad1.30x1.75mm_HandSolder | 1 | 33k

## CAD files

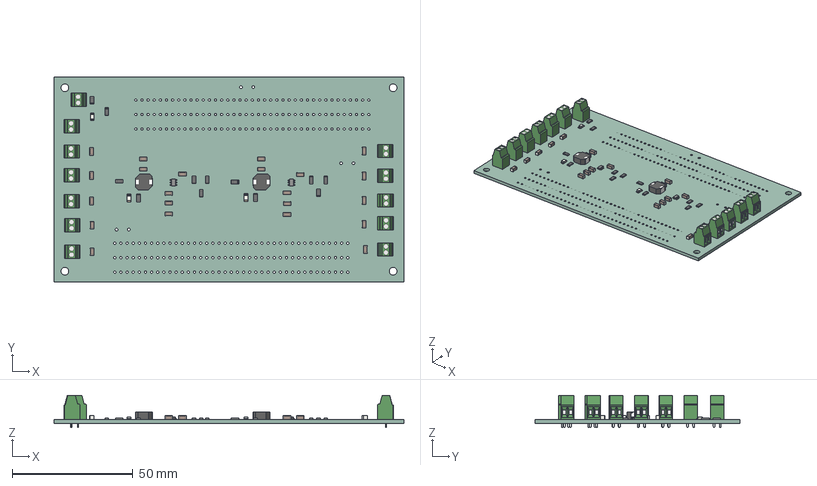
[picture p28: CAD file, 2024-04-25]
Documentation/Electrical/PCB/Sources/Power_Dist_Design/Power_Dist_Board/Power_Dist_Board.step
145.0 x 85.0 x 13.4 mm
Power_Dist_Board PCB

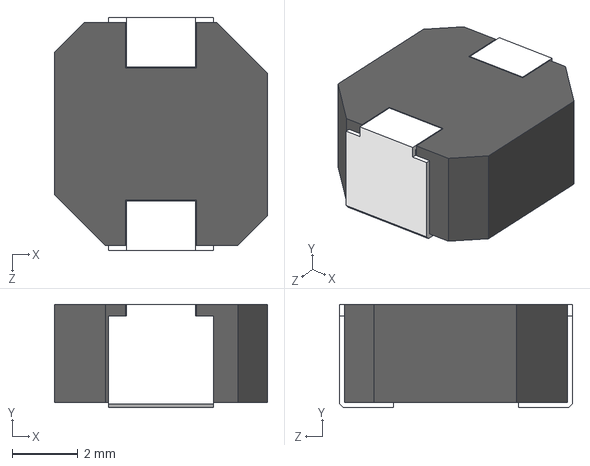
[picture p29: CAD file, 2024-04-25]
Documentation/Electrical/PCB/Sources/Power_Dist_Design/Power_Dist_Board/Component_Lib/3D_Models/TDK_Inductor.step
6.50 x 3.15 x 7.10 mm

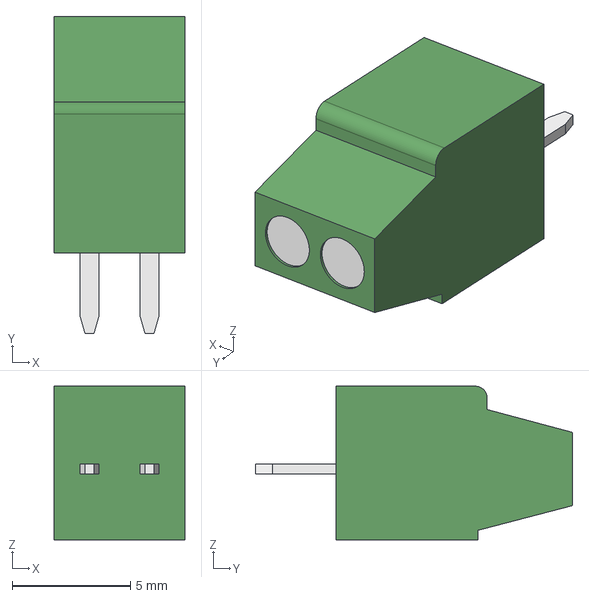
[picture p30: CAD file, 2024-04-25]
Documentation/Electrical/PCB/Sources/Power_Dist_Design/Power_Dist_Board/Component_Lib/3D_Models/397730002.stp
5.54 x 13.4 x 6.50 mm

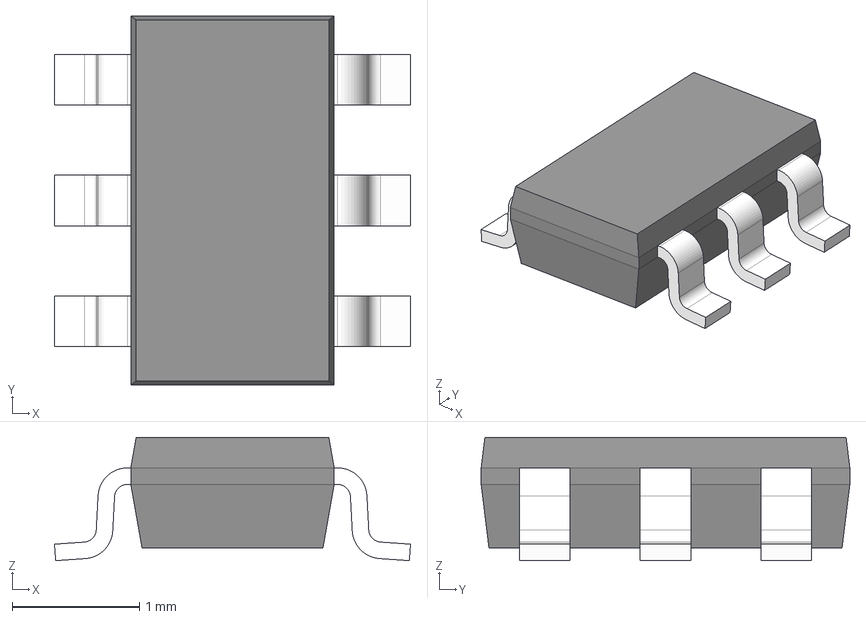
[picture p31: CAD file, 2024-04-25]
Documentation/Electrical/PCB/Sources/Power_Dist_Design/Power_Dist_Board/Component_Lib/3D_Models/TPS565201.stp
2.80 x 2.90 x 0.97 mm
BODY-SOT
LEAD-SOT x 6

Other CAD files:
Documentation/3D Models/Chassis/37d-gearmotor-10.ipt
Documentation/3D Models/Chassis/60mm Wheel hub.ipt
Documentation/3D Models/Chassis/60mm Wheel.ipt
Documentation/3D Models/Chassis/Chassis Frame Layout.iam
Documentation/3D Models/Chassis/Chassis Frame.iam
Documentation/3D Models/Chassis/Extruded Alumnium 250mm.ipt
Documentation/3D Models/Chassis/Extruded Alumnium 300mm.ipt
Documentation/3D Models/Chassis/Mock Battery.ipt
Documentation/3D Models/Chassis/Mock Charger.ipt
Documentation/3D Models/Chassis/Mock Gyro-Acc.ipt
Documentation/3D Models/Chassis/Mock I2C Bus.ipt
Documentation/3D Models/Chassis/Mock Motor Driver.ipt
Documentation/3D Models/Chassis/Mock PCB.ipt
Documentation/3D Models/Chassis/Mock Spacer.ipt
Documentation/3D Models/Chassis/Motor Attachment.ipt
Documentation/3D Models/Chassis/Revisions/Motor Attachment 2.0.ipt
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

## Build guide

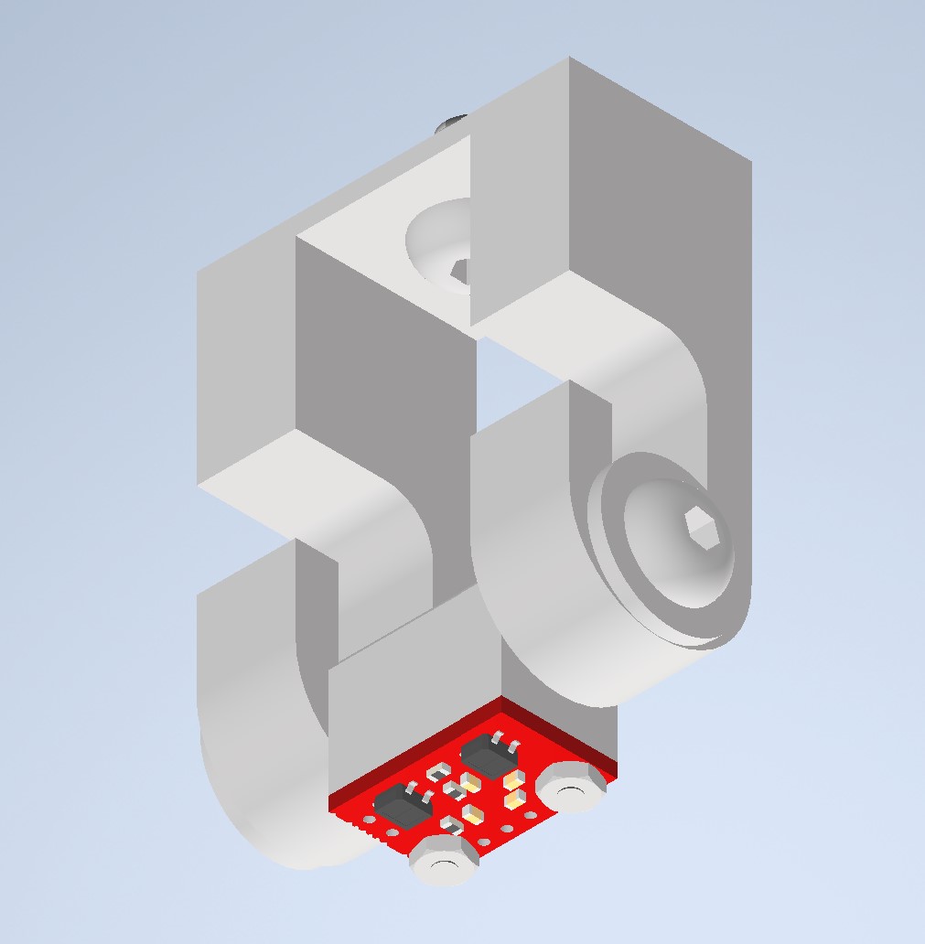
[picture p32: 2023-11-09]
Documentation/Images/Sign off Photos/Attachment/2 Sensor Assembly.jpg

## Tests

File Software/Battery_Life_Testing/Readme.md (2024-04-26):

The arduino file in this directory was used to record the battery voltage data over a 38 minute period. When run, it toggles a BJT connected to the power board and a DC power supply to emulate connecting and disconnecting the power board from a battery. It writes the voltage recorded on the analog in pin (used to record the 5 V bus) and the cycle number that it was recorded at to an SD card. When the voltage drops below a certain threshold, the arduino writes the cycle number that it occurred at to a different file on the SD card. This program was used to estimate the battery voltage, and more about it can be found in the power manual.

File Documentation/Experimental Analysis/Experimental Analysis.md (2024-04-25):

# Experimental Analysis

## Introduction 
The purpose of this report is to verify the requirements for the project and explain the procedures used to validate results. The results will be compared against the measures of success outlined in the project proposal to determine if the project was successful. This will also detail what the next steps are moving forward.

### Requirements

| Item | Constraint/Specification | Subsystem | 
|-|-|-|
| 1 | Shall design a robot with a single start button. Once activated, the robot will begin navigating its environment. | Power |
| 2 | Shall design a robot that possesses an allocated data input point for an alternative start method. | GUI |
| 3 | Shall design an autonomous robot that has customizable dimensions with the stock design only occupying up to one-half of the allowed cubic foot (1 ft x 1 ft x 6 in). | Chassis |
| 4 | Shall design a robot platform whose modules are plug-and-play adaptable for different IEEE competition requirements.  | Chassis, Attachments, Navigation|
| 5 | Shall design a robot that possesses a robust, centralized charging system that does not require the removal of the battery and that allows the robot to be used while being charged. | Battery Management |
| 6 | Shall evaluate wireless charging as an option for charging the robot. | Wireless Charging|
| 7 | Shall design a robot to possess a single emergency stop button that is accessible and stops all robot movement without removing power to essential processors. | Power |
| 8 | Shall design the power bus in such a way that the DC motors do not inhibit robot operation. | Power |
| 9 | Shall design a robot that can travel inclines and declines up to 25 degrees.  | Motors |
| 10 | Shall design a robot that can turn 360 degrees left and right and move forwards and backwards based on sensor inputs. | Motors, GUI |
| 11 | Shall design a robot whose navigation system controls movement; knows its location within a two-inch tolerance; and possesses a maximum speed of 2 feet per second. | GUI, Navigation, Location, Motors|
| 12 | The attachment components will be 3D printed to reduce cost of project. 	| Attachments, Layout and Organization |
| 13 | The line sensor attachment must be designed to place the sensor between 0.125 and 0.375 inches off the ground. | Attachments | 
| 14 | The frame will need to be able to withstand 20 pounds. | Chassis |

## Results

### Constraint 1 - Start Button

The first requirement is for the robot to have a functioning start button, which after activation will begin robot operation. This was tested 10 times by turning the switch off and then on again to see if the robot succesfully starts back up. The robot successfully turned on in 10 out of 10 trials.

| Trial Number | Robot Successfully Turned On |
|---|---|
| 1 | yes |
| 2 | yes |
| 3 | yes |
| 4 | yes |
| 5 | yes |
| 6 | yes |
| 7 | yes |
| 8 | yes |
| 9 | yes |
| 10 | yes |

As can be seen in the above table, the robot successfully turns on in 10 out of 10 trials, and so this constraint has been met.

Video demonstration of start switch demonstration can be found at ./Videos/Start_Switch.mp4

### Constraint 2 - Alternate Start Method 
This constraint was created since SECON has opportunities for teams to receive extra points for having an alternative start method, which is met in the [signoff for the master control](https://github.com/lchapman42/Control-Sensing-Wireless-Charging-Robot/blob/main/Documentation/Signoffs/IsaacJennings-Signoff-MasterControl.md). Since the alternate start method has a spot to be placed on the Jetson Nano, the constraint has been met.

### Constraint 3 - Dimensions
The dimensions of the robot are customizable when ordering the extruded alumnium for future teams. The extruded alumnium can be cut to change the dimensions. Additionally, the stock design only takes up the specified 1 ft x 1 ft x 6 in area shown below. This constraint could not be experimentally tested because it is inherently true.

##### Figure 1. Length (12 in)
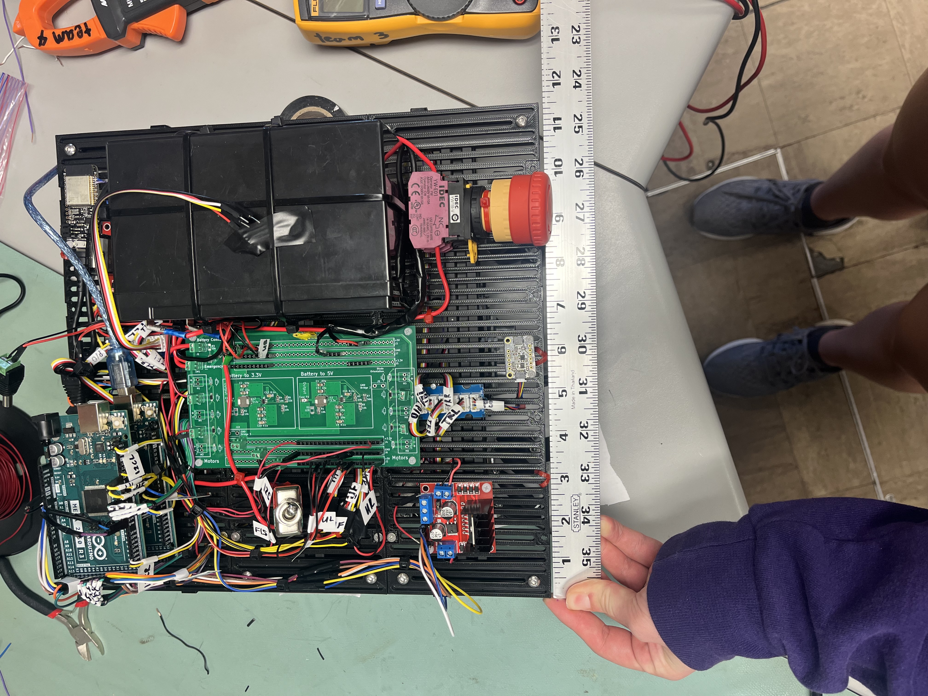
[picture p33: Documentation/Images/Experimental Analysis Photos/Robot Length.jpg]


##### Figure 2. Width (12 in)
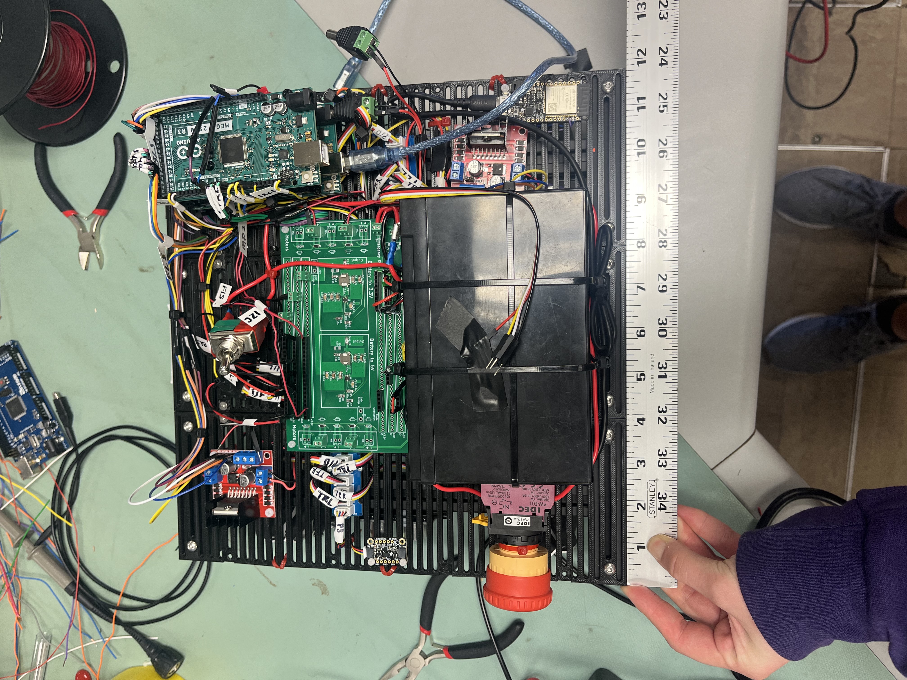
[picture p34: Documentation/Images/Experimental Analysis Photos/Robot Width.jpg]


##### Figure 3. Height (6 in)
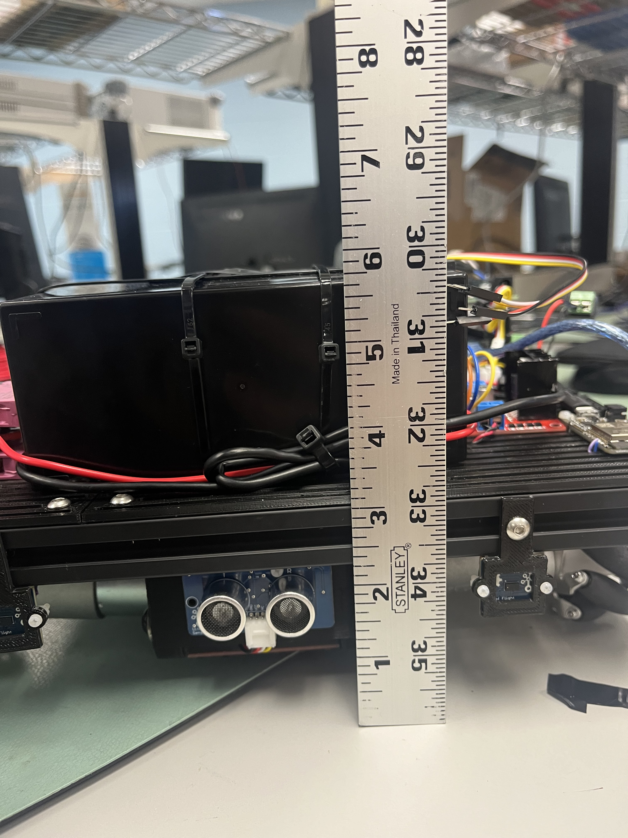
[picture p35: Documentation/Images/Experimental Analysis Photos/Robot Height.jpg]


Overall, the constraint was met.

### Constraint 4 - Plug-and-Play Adaptability
This constraint was derived from the goal of the project being to create a base platform for future teams. Therefore, the robot needed to be adapatable. For components, this is possibe due to drop-in t nuts utilized for any component directly attached to the frame. Also, a slotted sheet system was developed for any componets connected to the top of the frame. These allowed for versatility with movement of componets. Additionally, being able to reuse code and having functions avaliable for different sensors was created. Testing some measurable features of both are seen below. 
#### Wheel Movement (4 in)
This constraint does not have a true experimental analysis section. The picture below shows the 4 in movement capabilities if the base robot was needed to be reconfigured.
The front wheel can move 20 mm forward and 95 mm backward. The back wheel can move forward 95 mm and backwards 20 mm. Both wheels can move a total of 115 mm (4.528 in) and this will be the same on both sides.
##### Figure 1. Front Wheel Forward Movement Measurement
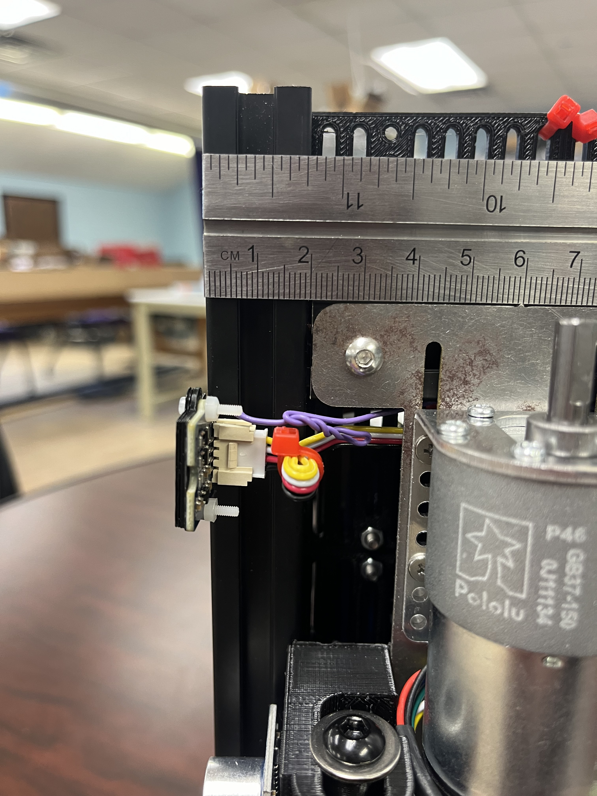
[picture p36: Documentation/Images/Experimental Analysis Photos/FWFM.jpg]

##### Figure 2 & 3. Front Wheel Backward Movement/Back Wheel Forward Movement Measurement
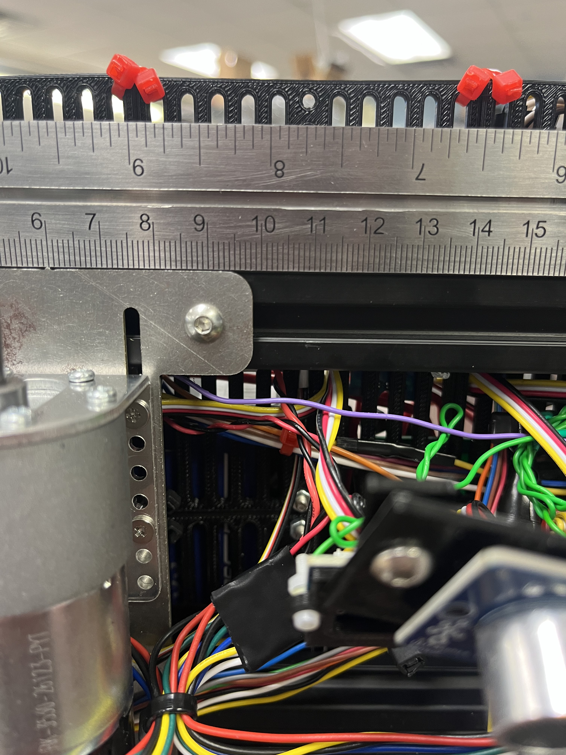
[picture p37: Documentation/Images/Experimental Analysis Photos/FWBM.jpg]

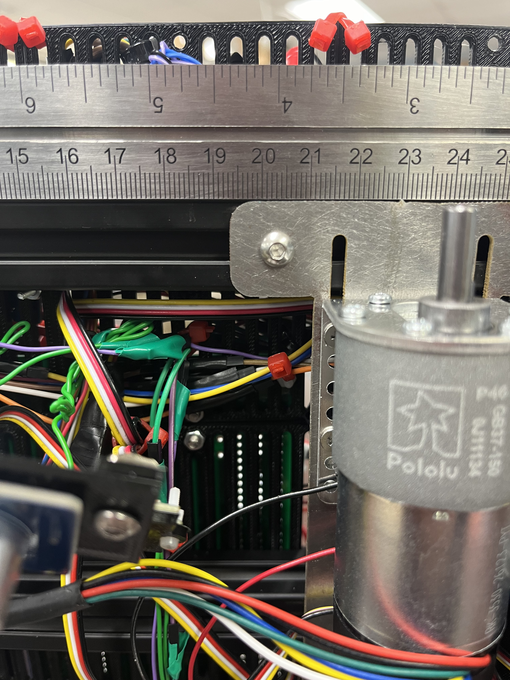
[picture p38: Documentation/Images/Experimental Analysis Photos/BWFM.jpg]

##### Figure 4. Back Wheel Backward Movement Measurement
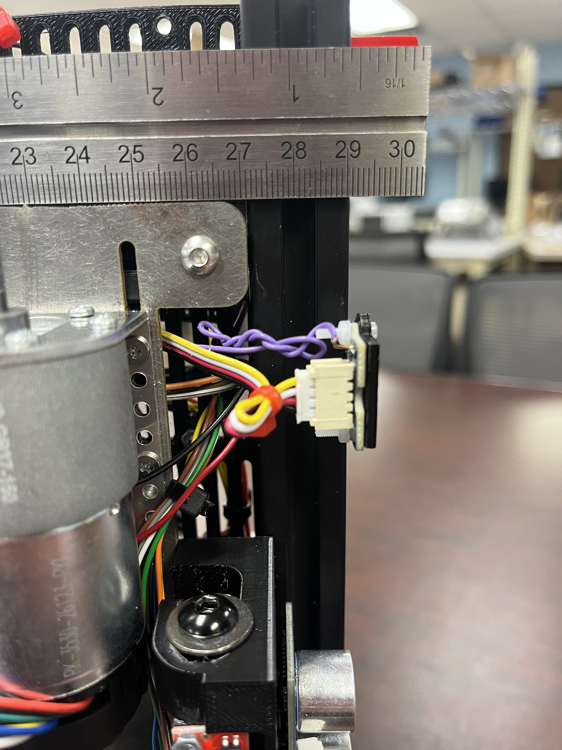
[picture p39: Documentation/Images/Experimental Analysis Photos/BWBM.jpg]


|Wheel| Does it move 4 inches? |
|-|-|
| FL | yes |
| FR | yes |
| BL | yes |
| BR | yes |

#### I2C Bus
The I2C bus constrait required that all I2C sensors be plug and play adaptable. To test this constraint the connections on the I2C bus will be scrambled, and data readings will be taken to show the readings are consistent throughout. The spots are differentiated by A (right side of robot) and B (left side of robot) for the two I2C busses. Each bus is split into 5 spots, for example A1 is the first slot of bus A.

See [Youtube Link](https://youtu.be/BVPlBgpR0Bg) for test

##### Trial 1 (No Movement)
|Sensor|Original Spot|Value|
|-|-|-
| 1 | A1 | 965
| 2 | A2 | 514
| 3 | A3 | 1020
| 4 | A4 | 969
| 5 | B1 | 774
| 6 | B2 | 165
| 7 | B3 | 161
| 8 | B4 | 983
##### Trial 2
|Sensor|Moved To|Value|
|-|-|-
| 1 | A2 | 965
| 2 | A1 | 533
| 3 | A4 | 962
| 4 | A3 | 1019 
| 5 | B2 | 160
| 6 | B1 | 769
| 7 | B4 | 979
| 8 | B3 | 160
##### Trial 3
|Sensor|Moved To|Value|
|-|-|-
| 1 | A4 | 971
| 2 | A3 | 1018
| 3 | A2 | 528
| 4 | A1 | 966
| 5 | B4 | 980
| 6 | B3 | 160
| 7 | B2 | 162
| 8 | B1 | 769

<br />
<br />

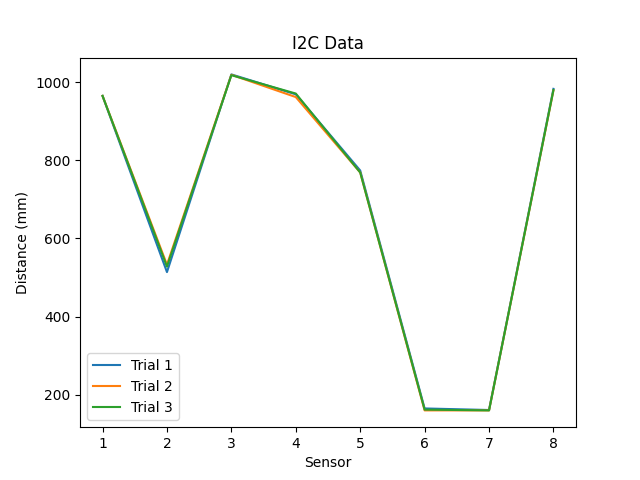
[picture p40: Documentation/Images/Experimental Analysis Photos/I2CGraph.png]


The data shows no change between trials. Three trials were ran because it is trivial in nature (electrically, nothing changes). The constraint of plug and play adaptability has been met.

#### Wire Grouping/ Labeling
This is not able to be experimentally measured because is it inherently true and can be seen in the picture below.



Overall, the constraint was met.

#### ROS2 Adaptable Code base
ROS2 is naturally inclined to easy adaptation, but a few extra common practice steps were taken to make adaptation even simpler. For one, all configuration files (.yaml, .urdf, .xacro
include their varying parameters at the top of the files for easy access without having to locate variables throughout the code. The unified robot description (URDF) was also broken into 
multiple XML macro (xacro) files for easy troubleshooting and modularity. If, for instance, the ultrasonic sensors weren't used, simply removing the ultrasonic xacro would remove all of the associated code
for any robot transforms. The serial communication packages also present modularity by containing function instances for each sensor type that can be easily removed or added to. Finally, all of the launch files are set
with the filepaths at the top of the file to allow quick changes for the robot. Essentially, the file systems in ROS2 have been set up as templates with parameters at the top of the entities. 

### Constraint 5 - Robust Charging System

This constraint required that the robot possess a robust, centralized, power system and had several requirements. The first requirement is that the power system be able to supply power to a 3.3 V and 5 V power rail successfully. To test this, the voltages at each voltage rail on the power board were measured for the total range of possible input battery voltages, which is between 11 and 14.6 V. This was done to show that the power board would operate as needed for any possible battery voltage. The data recorded is shown below. 

| Measured Input Voltage (V) | Top 5 V Rail (V) | Top 3.3 V Rail (V) | Bottom 5 V Rail (V) | Bottom 3.3 V Rail (V) |
| --- | --- | --- | --- | --- |
| 10.0013 | 5.0461 | 3.2792 | 5.0466 | 3.2792 |
| 11.0010 | 5.0491 | 3.2798 | 5.0490 | 3.2798 |
| 12.0014 | 5.0508 | 3.2802 | 5.0507 | 3.2802 |
| 13.0011 | 5.0524 | 3.2807 | 5.0524 | 3.2808 |
| 14.0008 | 5.0536 | 3.2811 | 5.0536 | 3.2811 |
| 15.0006 | 5.0547 | 3.2813 | 5.0546 | 3.2814 | 

| Trial | Successfully Charging While Running |  
| --- | --- |
| 1 | yes |
| 2 | yes |
| 3 | yes |
| 4 | yes |
| 5 | yes |
| 6 | yes |
| 7 | yes |
| 8 | yes |
| 9 | yes |
| 10 | yes |

Video of robot charging while running demonstration can be found at ./Videos/Charging_While_Running.mp4

The other specification required by this constraint has to do with the battery life. In the project proposal document, a requirement of a 2 hour battery life was set. After researching battery capacities, this requirement was then amended to 30 minutes of continuous battery life to make the requirement more realistic.

To test this, the robot was run with all of the motors running at maximum speed. A program was used that continuously rotated the robot in a circle without changing the robot position. This was done so that the robot's continuous battery life could be tested without having to readjust the robot's position and so that the robot did not change directions constantly, causing uneccessary stress on the motors and motor drivers. 

This program was run continuously in 10 minute intervals, between which the robot was turned off for a few minutes to allow for the motors and motor drivers to cool down to prevent overheating. The total elapsed time of the robot being on is what was recorded as the robot's continuous runtime battery life below. The voltage across the battery terminals was monitored to ensure that the battery did not drop below the minimum recommended voltage.

In testing, the battery voltage dropped similar to an exponential decay from around 14 V to about 13.13 V. At 13.13 V, it remained for 20 minutes before beginning to drop again. After turning the robot off, the battery voltage would increase slightly, to about 13.27 V, and began to decrease to about 13.13 V where it stayed.

The only component that was not present for the battery life testing that could make any different in battery life at all was the Jetson Nano. The arduinos, motors, and sensors, were all connected, powered up and running. Even with this consideration, the Jetson Nano is only running the Master control code and is not using some of its more power-hungry components like the GPU, and so should not change the battery life drastically.

Moreover, the battery life measured vastly exceeded expectations (as can be seen below), and so the Jetson Nano's presence should not make such a large difference that the battery life would fall below the constraint requirement.

There is a video demonstration of the battery life test that can be found in ./Videos/Battery_Life_Test.mp4

In the table below, the measured battery life is compared to the calculated worst-case battery life with all components continuously pulling the maximum current. The maximum current required was calculated at just over 10 A (there was a slight increase from what is listed in the Battery Management signoff due to forgetting to include Arduinos in the calculation). Using this current and the rated Amp-Hours of the battery, the estimate was calculated.

| Calculated Worst-Case Battery Life (hour:min:sec) | Measured Battery Life (hour:min:sec) |
| --- | ---|
| 0:43:11 | 3:05:31 |

At the time given, the battery still showed no signs of being close to depletion. The battery voltage stayed at the flat portion of the battery discharge curve for nearly 3 hours. Using the battery datasheet (can be found in the battery management signoff) and the time the battery took to discharge to the flat portion of the discharge curve, the experimental discharge curve was matched to the datasheet discharge curve and the battery life was estimated to be around 3 hours and 40 minutes.

### Constraint 6 - Wireless Charging

For this requirement, the prospect of wireless charging used to power and/or charge the robot over the full area of the arena had to be researched and the feasibility of which had to be evaluated. For wirelessly powering the robot over the full area of the arena, capacitive power transfer was deemed to be more suited, but is much more experimental as inductive wireless power transfer is the primary method used commercially.

In capacitive wireless power transfer, a transmitting sheet is placed underneath the device, which has a receiving sheet, making an effective capacitor between. The transmitting sheet is excited with high frequencies with the positive lead of a function generator and the negative lead is allowed to sit somewhere unconnected to anything. The receiving sheet is the connected to a quarter-wave transformer, which allows for a stray return capacitance beween the receiver and the negative lead of the driving function generator. More information on this can be found in the wireless charging signoff in Documentation/Signoffs.

With research and experimentation, it was found that a load on the robot could be wirelessly powered. A video of wirelessly powering an LED on top of the robot can be found in ./Videos/Wireless_Power.mp4.

With the demonstration of capacitive wireless power it was determined that wireless charging for the robot is plausible but will require more research, development, and precautions. 

The first reason for a need for more research is the power output. At best, with the "blue box" amplifier and small transmitting sheet in Dr. Van Neste's lab and no load attached, a current out of the receiving sheet of 1-2 A could be measured. In order for this to be used to power or charge a robot, the high-frequency signal (MHz range) will need to be shifted down to 60 Hz and/or rectified to DC in order to power electronics on the robot. With this in mind, it is unknown if the system will be able to output enough power that after component inefficiencies will be able to charge a battery or power the robot at all.

An additional factor that makes higher power more difficult is the potential for interfering with or damaging electronics onboard the robot. As the transmitter power increases, the potential for interferance and/or damage to electronics will require more robust shielding of electronics on board.

Another potential cause for concern is the significant safety precautions that will be required if this system is scaled up. With the small transmitting sheet and small load of an LED, the input voltage could be kept to a moderate 10 V peak-to-peak. However, as the transmitting sheet increases in size, the voltage required to power it increases very fast. Because of this, there will need to be significant insulation surrounding all energized metal sheets (primarily the transmitting sheet) to prevent injury. Additionally, there may be university rules and regulations that must be followed when using high voltages in a university laboratory.

With the above research and verification, this constraint has been met.

### Constraint 7 - Emergency Stop

The emergency stop requirement requires that the robot have a button that when pressed, power will be removed from the motors, but not the microcontrollers or sensors. In order for this to be considered successful, in 10 out of 10 trials, pressing the emergency stop button had to result in a complete shutdown of the motors while keeping all other components powered. To be considered successful, the voltage delivered to the motors must be withing 0.5 V of 0.0 V.

To test this, the robot was turned on with the motors powered. The emergency stop button was then activated to cut power to the motors. The voltage to each motors was then measured and the LED indicators on the microprocessors were visually verified to ensure that the motors would remain unoperational and the essential processors would remain operational. 

The voltages measured over 10 trials at each of the motors is shown below.

| Trial | Motor 1 Voltage (mV) | Motor 2 Voltage (mV) | Motor 3 Voltage (mV) | Motor 4 Voltage (mV) | Processors on?|
| --- | --- | --- | --- | --- | --- |
| 1 | 0.029 | 0.019 | 0.018 | 0.014 | yes |
| 2 | -0.002 | 0.003 | 0.009 | 0.008 | yes |
| 3 | -0.016 | -0.007 | 0.033 | 0.004 | yes |
| 4 | 0.005 | -0.002 | 0.002 | -0.006 | yes |
| 5 | -0.005 | 0.006 | 0.015 | 0.002 | yes |
| 6 | 0.004 | 0.001 | 0.006 | -0.002 | yes |
| 7 | 0.004 | -0.001 | -0.030 | 0.011 | yes |
| 8 | -0.013 | 0.009 | -0.009 | -0.008 | yes |
| 9 | 0.0015 | 0.017 | 0.033 | 0.020 | yes |
| 10 | 0.0028 | 0.030 | 0.027 | 0.034 | yes |

As can be seen above, all of the motor voltages when the emergency stop button was activated are well within 0.5 V of 0.0 V (especially after noting the units of mV, not V). Because of this, this constraint is considered to have been met.

Video of emergency stop button demonstration can be found at ./Videos/Emergency_Stop_Demo.mp4

### Constraint 8 - Back EMF

In order for this constraint to be considered successful, during motor operation the 3.3 V and 5 V rails must not suffer from counter-EMF from the motors. In order to be considered successful, the voltage buses must not drop to more than 80% of the nominal value. 80% was chosen so that the back-EMF would not be able to push a digital high value down below the threshold, turning high values into low values. This gives lower limits of 2.64 V and 4.0 V for the 3.3 V and 5.0 V buses, respectively.

To test this, the motors were turned on and off, and the voltages at each voltage rail were measured each time. This was done at different locations on the voltage buses for even greater rigorousness. 

The table below shows the measured voltages with and without motor operation.

| Trial | 5 V Rail Voltage with Motors Off (V) | 5 V Rail Voltage with Motors On (V) | 3.3 V Rail Voltage with Motors Off (V) | 3.3 V Rail Voltage with Motors On (V) |
| --- | --- | --- | --- | ---|
| 1 | 3.2580 | 5.0250 | 3.2575 | 5.0264 |
| 2 | 3.2575 | 5.0263 | 3.2575 | 5.0264 |
| 3 | 3.2575 | 5.0261 | 3.2576 | 5.0265 |
| 4 | 3.2576 | 5.0261 | 3.2575 | 5.0264 |
| 5 | 3.2576 | 5.0261 | 3.2575 | 5.0264 |
| 6 | 3.2576 | 5.0269 | 3.2575 | 5.0251 |
| 7 | 3.2574 | 5.0263 | 3.2566 | 5.0250 |
| 8 | 3.2576 | 5.0259 | 3.2566 | 5.0549 |
| 9 | 3.2575 | 5.0264 | 3.2567 | 5.0264 |
| 10 | 3.2577 | 5.0258 | 3.2575 | 5.0246 |

As can be seen above, the voltages both with and without motor operation are well above the lower limit and will function with no issue for digital high values. Therefore, this constraint has been met.

Adding 0.1 uF capacitors directly to the motor driver outputs was also experimented with. It is recommended by the Pololu to add 0.1 uF ceramic capacitors between the motor terminals as close to the motors as possible to reduce noise and back-EMF. With no capacitors, the 12 V rail voltage dropped between 0.1-0.5 V when the motors changed direction from full speed in one direction to full speed in the opposite direction. The addition of capacitors to the motor driver outputs did not seem to have a noticeable impact on the voltage drop with a change in motor direction.

### Constraint 9 - Inclines/Declines
This constraint was created since the 2024 SECON board has a 25 degree incline and decline. This was tested 10 times by having the robot travel up and down a hill in forward and reverse motion. 

| Trial Number | Robot Successfully Ascended and Descended the Hill |
|---|---|
| 1 | yes |
| 2 | yes |
| 3 | yes |
| 4 | yes |
| 5 | yes |
| 6 | yes |
| 7 | yes |
| 8 | yes |
| 9 | yes |
| 10 | yes |

As can be seen in the above table, the robot successfully traverses the hill in 10 out of 10 trials, and so this constraint has been met.

Video demonstration of start switch demonstration can be found on [this video](https://youtube.com/shorts/sC5Fqg60_ig?feature=share)

### Constraint 10 - Motor Control

The robot was tasked with moving 360 degrees as well as forwards and backward to show it can fully navigate and roam in any environment, and it must be able to do so based on sensor inputs. This was tested by having the robot sweep the 2023 SECON board which was similar to how it was navigated for competition, and we also had the robot follow a line and return to the starting point.

[This video](https://youtu.be/3MeIy1WahUA) shows the robot navigating the 2023 board using the ultrasonic sensors. 
[This video](https://youtu.be/stM9KGa8I_E) shows the robot following a line, turning around, and following it back to the start.

The robot was successful in navigating both courses, so the constraint was met.

### Constraint 11 - Navigation

#### Navigation
This constraint was created because the robot needs to be able to autonomously navigate the board for a SECON competition. This was tested by having the robot sweep the 2023 SECON board and follow a line similar to the 2022 and 2024 boards.

[This video](https://youtu.be/3MeIy1WahUA) shows the robot navigating the 2023 board using the ultrasonic sensors. 
[This video](https://youtu.be/stM9KGa8I_E) shows the robot following a line, turning around, and following it back to the start using the line-following sensors.

The robot was successful in navigating both courses, so the constraint was met.

##### **Object Detection**

See [Youtube Link](https://youtu.be/_iFhnvbLboQ) for Object Detection

| Trial Number | Object Successfully Detected |
|---|---|
| 1 | yes |
| 2 | yes |
| 3 | yes |
| 4 | yes |
| 5 | yes |
| 6 | yes |
| 7 | yes |
| 8 | yes |
| 9 | yes |
| 10 | yes |

Object was sucessfully detected 10 out of 10 trials. Constraint is met.
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

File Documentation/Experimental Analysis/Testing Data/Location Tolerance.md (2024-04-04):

Tables of the Equations and Test Data for Location Tolerance - Constraint 11
<br />
<br />

<div align="center">
Table 1: The Equations Used to Measure Error (mm)
</div>

<div align="center">
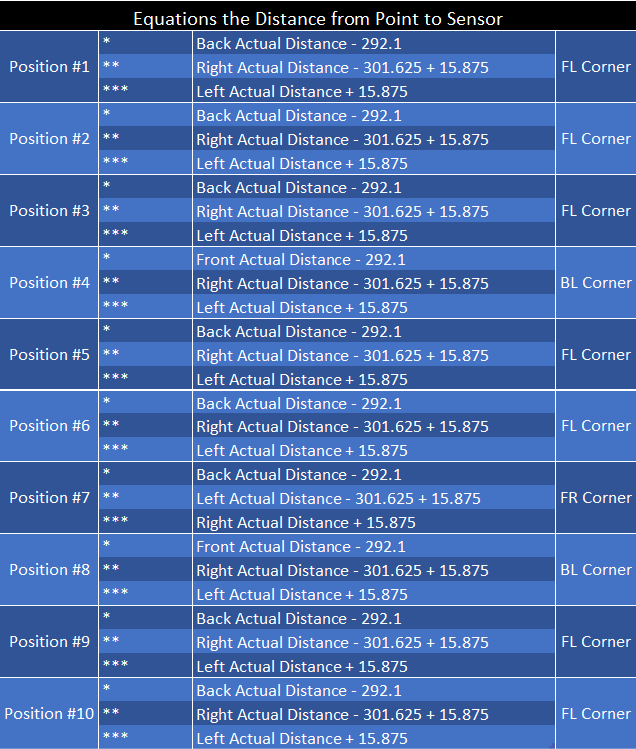
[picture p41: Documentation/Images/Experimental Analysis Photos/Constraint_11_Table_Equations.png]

</div>
<br />
<br />
<br />

<div align="center">
Table 2: Actual and Measured Distances for Position 1 - 5
</div>

<div align="center">
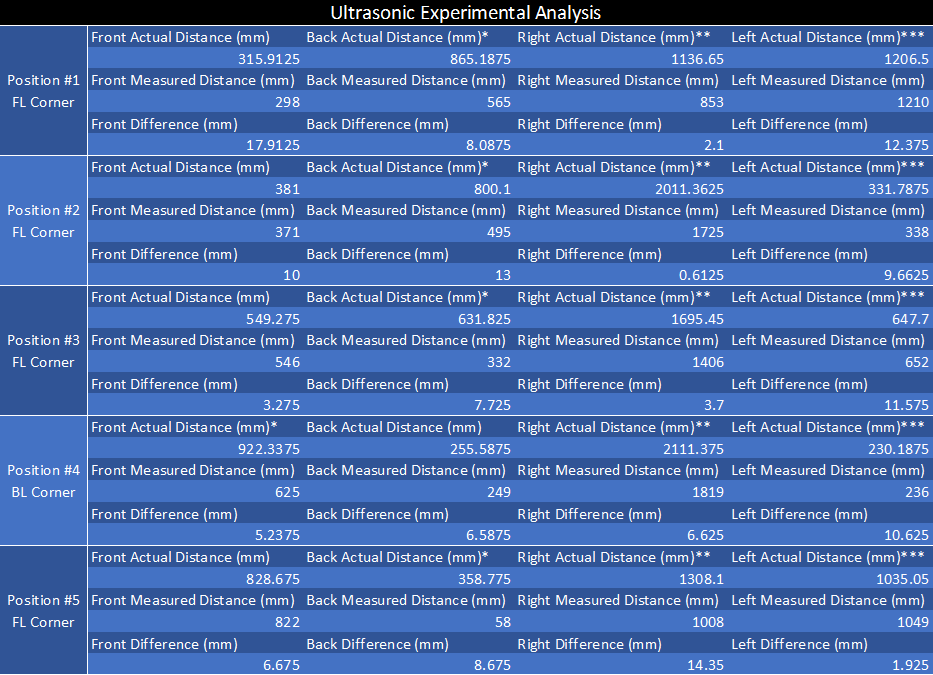
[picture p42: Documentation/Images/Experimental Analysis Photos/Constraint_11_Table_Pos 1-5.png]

</div>
<br />
<br />
<br />

<div align="center">
Table 3: Actual and Measured Distances for Position 6 - 10
</div>

<div align="center">

</div>

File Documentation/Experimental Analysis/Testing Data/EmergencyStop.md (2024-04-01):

Table 1. Results from Testing Emergency Stop Button
|Trial | Motor 1 Voltage | Motor 2 Voltage | Motor 3 Voltage | Motor 4 Voltage | Processors on?|
| --- | --- | --- | --- | --- | --- |
| 1 | 0.000 | 0.000 | 0.000 | 0.000 | yes |
| 2 | 0.000 | 0.000 | 0.000 | 0.000 | yes |
| 3 | 0.000 | 0.000 | 0.000 | 0.000 | yes |
| 4 | 0.000 | 0.000 | 0.000 | 0.000 | yes |
| 5 | 0.000 | 0.000 | 0.000 | 0.000 | yes |
| 6 | 0.000 | 0.000 | 0.000 | 0.000 | yes |
| 7 | 0.000 | 0.000 | 0.000 | 0.000 | yes |
| 8 | 0.000 | 0.000 | 0.000 | 0.000 | yes |
| 9 | 0.000 | 0.000 | 0.000 | 0.000 | yes |
| 10 | 0.000 | 0.000 | 0.000 | 0.000 | yes |

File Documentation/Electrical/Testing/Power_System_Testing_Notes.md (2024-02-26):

These are my notes from testing the power system. They may also be useful to future teams using this system.

-- Luke 

## Notes from Weighing

Chassis - 5 lbs, 12 oz
Battery - ~< 2 lbs

## Notes from PCB, Battery, and Motor Testing - 2024-02-22

------------

Today with the motors mounted, the power PCB and battery were tested. The system was tested by adding the motors one by one, first with a power supply supplying the power to the board, then with the battery.

The motor speed is controlled in the Arduino code on a scale from 0 to 255.

With 1 motor connected at max speed, the board pulled 0.22 A.

Setting motor intensity below ~50 does not seem to turn the motors on.

With 2 motors connected at max speed, the current jumped to >1 A and settled to ~0.41 A.

Port 4 on the bottom Arduino Mega is bad and should not be used. Switched to port 7.

With all 4 motors connected at max speed, the the current spiked to ~2.8 A, then settled to ~0.8 A.

Voltages across motor terminals on board had no noticeable change when turning on/off the motors at max speed. It would be interesting to see the current through the protection diode to see if that is why, but that may be difficult to see.

The arduino mega has the following options for input power: barrel jack, USB connector, Vin port, and 3.3/5V ports. 

The barrel jack is 9 V, and the power board has no easy way of supplying that. The USB connector is 5 V, so with some cable modifications could be used from the board, but will need someone to modify a cable first (not hard but we need an extra one). The 3.3/5V pins can be used but are not recommended by Arduino. Finally, the Vin pin is another option, but the Arduino website says that the input voltage must be 7-12 V. This is not optimal since the battery is very rarely below 12 V. We decided to test powering the Arduino through the Vin pin from the 5V rail on the power board, and it worked with absolutely no issues. Will ask Roberts if there is any reason not to, but at least until a USB plug is used this seems like the best method.

Overall the battery and board performed perfectly, and the battery lasted around 3 hours of intermittent testing and still had plenty left.

## Notes from PCB and Battery Testing - 2024-02-03

------------

So far the PCB, battery, and battery charger have performed very well to testing.

Testing if board will output correct voltages (3.3 V and 5 V) over the entire possible input voltage range.

From the battery datasheet, recommended voltage range is between 11 V and 14.6 V.

Output voltages were measured at both the top and bottom voltage rails. Note that "top" and "bottom" refer to the rails shown as top and bottom in the orientation of every image of the board. Also, the "Battery to 3.3/5 V" text will be upright in this orientation. (Not that this matters that much because both worked).

| Measured Input Voltage (V) | Top 5 V Rail (V) | Top 3.3 V Rail (V) | Bottom 5 V Rail (V) | Bottom 3.3 V Rail (V) |
| --- | --- | --- | --- | --- |
| 10.0013 | 5.0461 | 3.2792 | 5.0466 | 3.2792 |
| 11.0010 | 5.0491 | 3.2798 | 5.0490 | 3.2798 |
| 12.0014 | 5.0508 | 3.2802 | 5.0507 | 3.2802 |
| 13.0011 | 5.0524 | 3.2807 | 5.0524 | 3.2808 |
| 14.0008 | 5.0536 | 3.2811 | 5.0536 | 3.2811 |
| 15.0006 | 5.0547 | 3.2813 | 5.0546 | 3.2814 |

Battery voltage started almost exactly at nominal 12.8 V.

Battery Charger LED Color Legend:\\
Green - Charged\\
Red - Charging\\
Red Flashing - Fault\\
Off - Off

Tested charging current - charging current starts at ~6 A, then drops exponentially to around 4.9 A. This is good because max charging current of battery is 7.2 A and charger can output up to 15 A, putting charger well within the acceptable range.

Battery took around 1 hour to completely charge. Charged in the typical capacitive curve with the battery voltage shooting up to 13 V and then 14 V very quickly and then very slowly to ~14.5 V. Once the battery was fully charged, LED turned green and the charger stopped supplying power.

Once the battery was fully charged or the charger was disconnected, the battery voltage began to fall back to somewhere in the 13 V range. Looking around online, it seems that this is normal and as long as it does not fall to far is perfectly ok.

Short Circuit Protection:\\

Tested charger short-circuit protection, taking the leads of the charger with no load and shorted them. Charger enters fault state. It appears that the charger has to be power cycled to reset it afterwards, but does so without issue. Charger does need to be unplugged for several seconds before the LED turns off, after which it can be plugged back in. 

Charger claims to have short circuit protection, and I thought that shorting the battery was a large enough risk to test it. The battery while connected to the charger was very briefly shorted to see what would happen. Nothing broke, though it took surprisingly long for anything to happen (~1 s). The battery was depleted a little and the charger began charging again. Did not enter fault state, do not know why.

Powering board from battery:

The board was perfectly functional when only powered by the battery, output the correct voltages. 

Connecting the charger to the battery while the battery (and charger) powered the board worked pretty much exactly as expected. The board functioned fine, and the battery would supply power with no issue. When the battery would become a little depleted, the charger would switch to charging mode, and charge the battery for a few seconds, then switch back to charged mode. Granted this is only with a small load, but this is a good sign.

Board under load:

The board worked perfectly fine under a small load (100 Ohms connected to each rail). A small load was used because the current capabilities are currently (haha) the biggest unknown. I realized that I can't test the full current capabilities using just resistors as of right now, since none of my resistors are able to tolerate even close to the power that will be dissipated at such high currents (5+ A). So for future tests will just need to wait for rudimentary motor control to be completed and then test that way, or think of a different device that can pull variable current, or find high-power, low resistance resistors.

Inductor Noise:

Measured the voltage across the inductors on an oscilloscope, did not take a picture but shape is similar to a decaying sinusoid that spikes periodically and then decays. A similar pattern (but much more attenuated) was found when measuring voltages between arbitrary points in the ground bus. This means that inductor noise may be an issue, but I am unsure if it will be so far.

Misc:

I found out that the chassis-mount connector meant to be screwed into the chassis and bridge beween an exterior cable and interior cable to the charger does not fit. The male side of the connector does not fit the female side of the cable.

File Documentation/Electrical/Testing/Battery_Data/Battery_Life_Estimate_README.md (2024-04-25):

The battery life was estimated using the following procedure.

Battery voltage data was taken in approximately 10 minute sections to form the dataset shown in battery_plot.svg. The plot of this was then given a transparent background and placed ontop of the datasheet battery curve given for the battery. The experimental data image was scaled to match the datasheet image, and it was found what percentage the experimental data ended at by matching the data to the curves on the datasheet. The data lasted for about 38 minutes, and given the overlaid image, appears to be at about 10-12% battery life. This gives an 80% battery life estimate (time to deplete the battery by 80% since 100% depletion will damage the battery) of between 3 hours 56 minutes and 4 hours 55 minutes.

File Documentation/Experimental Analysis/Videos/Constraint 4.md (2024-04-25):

Youtube Link for Constraint 4<br />

[Plug and Play Adaptability](https://youtu.be/BVPlBgpR0Bg)

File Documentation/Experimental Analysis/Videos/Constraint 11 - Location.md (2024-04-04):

Video Link for Constraint 11 - Location

[Location Tolerance for Position #6](https://youtube.com/shorts/rvX_kzKgJGA)

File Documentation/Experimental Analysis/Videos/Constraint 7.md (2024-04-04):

[Constraint 7 Videos - Youtube Link][def1]

[def1]: https://youtube.com/shorts/l9e4c29TDoM

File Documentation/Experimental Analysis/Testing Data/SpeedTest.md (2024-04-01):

Table 1. Results from Testing Robot Speed
|Trial | Distance Travelled | Speed (ft/s) |
| --- | --- | --- |
| 1 | 7' 4" | 0.733 |
| 2 | 7' 3" | 0.725 |
| 3 | 7' 3.5" | 0.729 |
| 4 | 7' 3.5" | 0.729 |
| 5 | 7' 4" | 0.733 |
| 6 | 7' 4" | 0.733 |
| 7 | 7' 3.5" | 0.729 |
| 8 | 7' 3.5" | 0.729 |
| 9 | 7' 4" | 0.733 |
| 10 | 7' 4" | 0.733 |

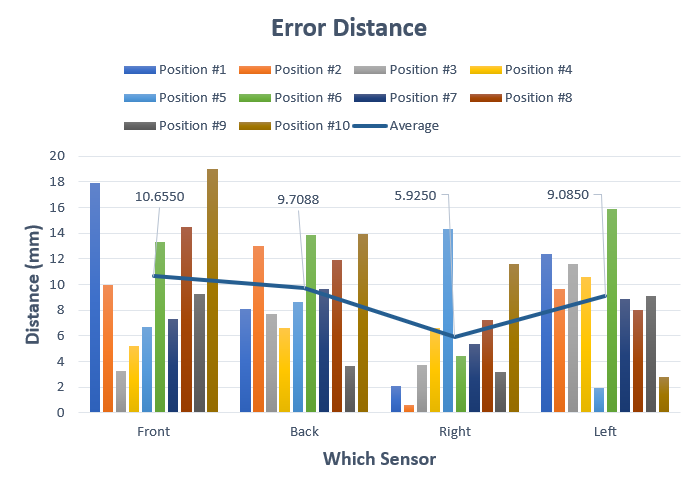
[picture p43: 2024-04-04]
Documentation/Images/Experimental Analysis Photos/Error Distance for Location Tolerance.png

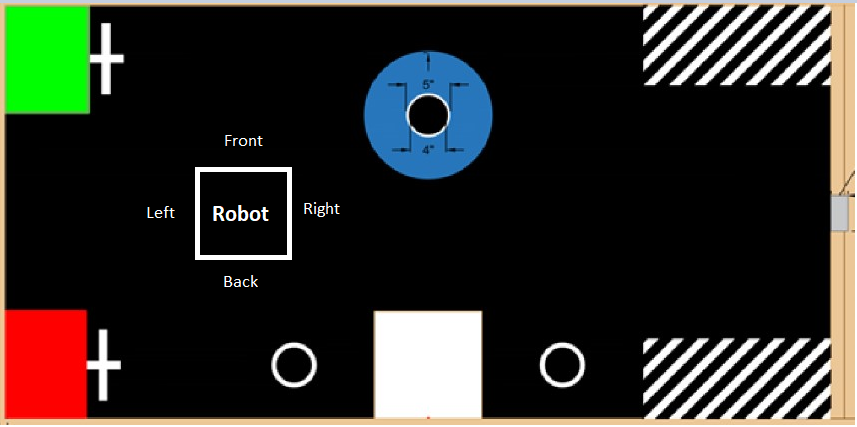
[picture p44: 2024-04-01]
Documentation/Images/Experimental Analysis Photos/2023 SECON Borad with Robot.png

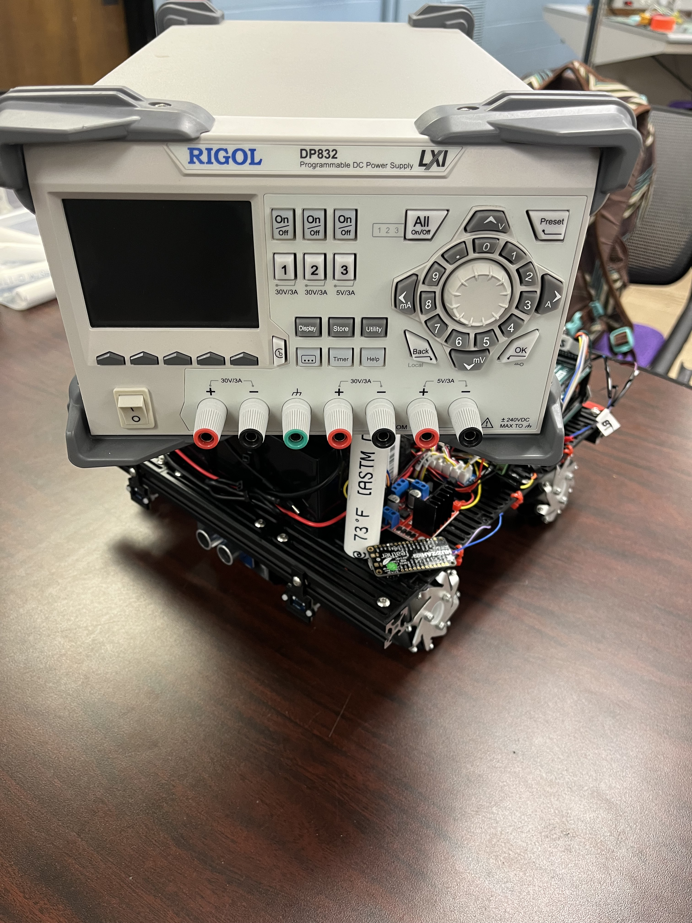
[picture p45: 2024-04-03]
Documentation/Images/Experimental Analysis Photos/Frame with Weight.jpg

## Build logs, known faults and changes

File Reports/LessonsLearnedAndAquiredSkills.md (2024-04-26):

# Lessons Learned

## Luke Chapman

Reflect on the project, both technical and organizational. What went well? What didn’t go well? 

- For the most part the power-related subsystems went well. The power distribution PCB performed adequately and passed all tests. The battery life vastly exceeded expectations. The wireless charging subsystem has the potential for future growth, but will require much more research and development. The largest oversight in the entire power system was the inclusion of reverse-biased diodes at the outputs of the 12V rail on the power board. In the case of a single-directional motors, this may be fine, but in the case of bi-directional motors this could cause issues as voltage polarities switch. At best this would lower the efficiency of a motor and at worst cause a component failure. Organizationally the team was very efficient and communicated very effectively. There were some issues that arose from some subsystems waiting on other subsystems to be finished before beginning development, but for the most part those issues were avoided as much as possible.

What unanticipated problems occurred? 

- There was a motor driver failure that we do not have 100% confirmation for the suspected cause of, but are quite certain is what happened. When running the robot back and forth repeatedly to test the battery life, the motor drivers got extremely hot. This is because the motors were switching directions about once per second, and when motors switch directions they send a very large voltage spike back into the driving circuitry. This got something very hot on the motor driver, and some component failed. After getting a new driver and changing the battery-life test program to a continuous robot rotation there were no more issues. A small issue found was that the screw terminals are a bit fragile. If hit from the front (opening side), the screw terminal leads will bend very easily, so different choices in the future may be a good idea.

What would you do differently if you were to do it over again? 

- If I were to do it over again I would have done a little more research into the wireless power transfer subsystem. Because not all of the aspects of that subsystem were thought out, only a very basic proof-of-concept could be demonstrated by the end.

What “best practices” have you identified? 

- One of the best practices I identified was in PCB design (in other areas as well) to make things as modifiable and adaptable as possible. This is particularly important in PCB design, where real board-level modifications are very difficult if that idea was not designed into the board. For instance: all of the motor terminals have an optional component place at the output. When it was realized that diodes were the wrong choice, capacitors could be swapped out very easily. Another example was that the choice of making rows of through-hole connectors for the output voltage rails allowed for very easy additions and changes to be made for different component connections (e.g. adding more pin connectors, screw terminals, etc.).

What words of wisdom would you pass on to future students?

- If you are doing a design in the first semester to be tested in the second, especially if it is something foundational: DO YOUR HOMEWORK. It will save you time in the long run. I checked and double checked everything, from the current capacities of the traces on the PCB to the SPICE simulations of the buck converters. I credit this to not having any failures in the power board, and while it took a lot of work in the first semester of Capstone, it saved me and my team an lot amount of additional stress in the second semester.

What new knowledge or skills did you acquire throughout capstone.

- PCB Design
- Trace current capacity calculations
- Ground isolation between motors and other components
- Back-EMF Mitigation
- Basics of Capacitive Wireless power transfer
- Being a part of a project with distinct subsystems

What classes have you taken that helped you in capstone? What did they help with?

- Electronics: Electronics taught me a lot of the basics of electronics and more advanced electronics circuits and devices. For example, how a buck converter works can be understood through what we learned in this class. Finally, developing a more sophisticated understanding of circuit analysis helped me to analyze and develop circuit layouts for the power board.
- Signals and Systems: In signals and systems we were taught about the basics of different types of electric signals. This was useful for understanding how a buck converter switching waveform operates. We were also introduced to reading datasheets in this course, which helped in the layout of the power board.
- Electromagnetics I and II: Electromagnetism played a role in several parts of the power subsystem. The wireless power transfer is an explicitly electromagnetics topic, and required knowledge of electromagnetics for development and research. Additionally, the potential interference of an inductor into other circuitry is understood through electromagnetics and so having some knowledge helped me in that regard as well.
- Intro to Digital Systems: In this class we learned the basics of digital logic and digital circuits. This was helpful in that it taught me about the voltage levels functionality required for the power board to be able to be used as a high or low value for digital circuit operation.

## Reid Crews

Reflect on the project, both technical and organizational. What went well? What didn’t go well? 

- For technical part of project, the team work well to complete the tasks individually and together with their unique skill set and knowlwdge.
- For organizational part of the project, the team was efficent in meeting and complete tasks except for a few misunderstandings.

What unanticipated problems occurred? 

- The library for the Grove Time of Flight Sensor (VL53L0X) did not allow to set a different address because it was privated in the class. I had to find a different library to set a different address because two I2C devices with the same address can not work at the same time.
- The I2C bus encountered a low voltage when ran at 5V, but not on 3.3V. This caused our sensors to read maximum values until switching to 3.3V

What would you do differently if you were to do it over again? 

- I would make a custom PCB for the I2C hub and connections for all the sensors to be easier to plug in play adaptable.
- Use a different brand/company for the Time of Flight (VL53L0X).

What “best practices” have you identified? 

- Using print statements in the code to debug issues is a great practice. It allows to see how the works and eliminate possible problems.

What words of wisdom would you pass on to future students?

- Research and collect many solutions to solve your problem, and then use pros and cons to compare all of your solutions. Use the criteria of money, time, complexity, and feasibility to make the correct decision.

What new knowledge or skills did you acquire throughout capstone.

- Understanding I2C communication
- Testing and Debugging Problems
- Understanding Technical Documentation
- PID Controller

What classes have you taken that helped you in capstone? What did they help with?

- CSC 1300, CSC1310, ECE3130, ECE4140 helped in programming, structure, and debugging
- ECE/ME4370, ME4140, ME3610 helped with mechanical and electrical application
- ECE4210 helped with the PID controller

## Isaac Hoese

Reflect on the project, both technical and organizational. What went well? What didn’t go well? 

- The bluetooth data transmission and sensors went smoothly.

What unanticipated problems occurred? 

- The I2C bus encountered a low voltage when ran at 5V, but not on 3.3V. This caused our sensors to read maximum values until switching to 3.3V
- The back line following sensor was shorted. However, the robot runs equally as well with only the front line following sensor active.

What would you do differently if you were to do it over again? 

- I would have combined the Arduino Mega and ESP32 onto a custom PCB. This would eliminate most of the wires on the robot (or at least made them much shorter) since the pin headers could be placed in ideal spots for our specific robot.

What “best practices” have you identified? 

- I think the main "best practice" was adopting the universal coding conventions which will allow future users to easily adopt code. Using the coding conventions also eliminates ambiguity between integer types ( uint32_t, uint16_t, etc.) and makes variable allocation an easier process.

What words of wisdom would you pass on to future students?

- Do as much research on your topic as you can up front. In hindsight, we could have chosen one sensor for navigation rather than the 14 that we have on the board. The more you research upfront the less work you will have to do in the long run.

What new knowledge or skills did you acquire throughout capstone.
- Basic ROS knowledge (From helping Isaac J.)
- Wireless Data Transmission
- GUI creation
- PID programming

What classes have you taken that helped you in capstone? What did they help with?

- CSC 1300, CSC1310, ECE3130, ECE4140 all helped with microcontroller programming and code structure
- ECE4370 for integrating mechanical and electrical systems
- ECE2050 for basic electrial knowledge for evaluating datasheets

## Isaac Jennings

Reflect on the project, both technical and organizational. What went well? What didn’t go well? 

- Overall, the project went well, but there were some things that better than others: in the master control subsystem, simultaneous mapping in ROS2 was achieved and was properly 
organized for future teams to use with very minor changes. Future teams can easily pick up where we left off and continue developing the next iteration of the project. 

What unanticipated problems occurred? 

- Connection with the Jetson Nano proved very difficult due to a lack in understanding of networking connections. The issues were resolved by dual booting Ubuntu on my laptop and 
connecting via CAT5 cable. 
- We also ran into problems establishing ROS's base_scan and odom sources. ROS requires either LIDAR or GPS for base_scan and either an IMU or LiDAR for odometry, so we utilized a 
previously used rplidar a2m8 to establish these transforms. 

What would you do differently if you were to do it over again? 

- I would say the most important change would be to use ROS supported sensors. Having ROS drivers would save a lot of time adapting between the two, and I would recommend future teams
utilized a one or more LiDAR sensors

What “best practices” have you identified? 

- Use ROS enhancement protocols (REPs). This will make the code easy to follow for future teams. Also, name systems intuitively. This is crucial for reproducibility.  

What words of wisdom would you pass on to future students?

- If your team decides to use ROS, start learning early. It is a sharp learning curve, but if you have the time to invest, it is possible to learn well enough to make improvements.
Also make documentation an even bigger deal. Add to the user manual we created this year and tell the next team to continue adding. It may take many years to create a code base that enables
very competitive ROS bots consistently. 

What new knowledge or skills did you acquire throughout capstone.

- I learned a ton about ROS middleware. My research and learning helped me to get a job working with ROS that quickly increased my knowledge and skills. I also learned a little bit of 
Object Oriented Programming (OOP). In addition to the hard skills, I also got a lot better at conflict management and team communication. 

What classes have you taken that helped you in capstone? What did they help with?

- CSC 1300 (Intro to programming) and 1310 (Data Structures and Algorithms): Basic programming knowledge for working with ROS2
- Microcomputer Systems: Helped with making serial connection witht he Arduino microcontrollers. 

## Abigail Kennedy

Reflect on the project, both technical and organizational. What went well? What didn’t go well? 

- Our team structure seemed to work well since we were able to agree on most things and conflicts were short-lived. However, there seemed to be some communication issues where problems would come up and not be discussed until it was too late.
- On the technical side, the team did well with specializing in different areas while still being knowledgeable of everyone's work which was useful when combining work in the building and testing stage.

What unanticipated problems occurred? 

- There were several problems with our constraints or measures of success where we weren't able to fully complete them, so we had to work with our advisor to modify them.
- The robot went slower than I expected which was part of my section, and I had to find was to test the robot to determine the root cause.

What would you do differently if you were to do it over again? 

- I would have ensured we had better communication to know where everyone was at on their part of the project so we could all encourage and help one another more easily.

What “best practices” have you identified? 

- Document everything - especially in the testing phase - to make sure you aren't wasting time repeating tasks
- Be organized for documents and the project since it speeds up a lot of work

What words of wisdom would you pass on to future students?

- Make sure to take your time in the planning phase and understand everything that you're doing
- Communicate everything with your team good and bad

What new knowledge or skills did you acquire throughout capstone.

- Team and project leadership
- Technical knowledge of motor control and mecanum wheel movement
- How to do electrical schematics
- How to give a good technical presentation

What classes have you taken that helped you in capstone? What did they help with?

- ECE 4370 - Mechatronics showed me the basics of motor control and how to integrate software with different physical components.
- ECE 2050, 3050, 4050 - All of the circuits and electronics classes came into play when determining how components should interact regarding different voltages and currents.
- ECE 3920 - Professionalism helped me determine how to give a better technical presentation, make ethical decisions, and work in an engineering team.

## Mabel Olson

Reflect on the project, both technical and organizational. What went well? What didn’t go well? 

- On the technical side of the project, I felt like my team was extremely well rounded and this allowed for easy distribution of work to people and allowed everyone to enjoy what we did. I also felt like us being well rounded allowed for a really smooth integration and experimentation portion of our project.
- Overall, I think the organization portion of our project went well. Towards the end there were some concerns that were brough forward, but it was too late to fix them. It stemmed from some poor communication between the group throughout the project that was never addressed. 

What unanticipated problems occurred? 

- With the motor attachment, there were problems with getting them made out of PLA and being a certain thickness due to a height contraint. Where the attachment was too thin/too weak, it caused bowing on the motors on the frame of the robot. I tried a new design with the same material and it also did not work. Therefore, I had to contact the machine shop to create the attachment out of metal instead. Over two iterations, the mount worked and we could proceed on with building. This caused a slight delay in progress for the robot in January. 

What would you do differently if you were to do it over again? 

- I would communicate more clearly every step of the project and through every concern to ensure there were no misunderstandings and more exact expectations layed out.
- I would have looked more best uses or suggestions for 3D printing componets to avoid needing to do as many iterations of designs and prints. 

What “best practices” have you identified? 

- For 3D models, more adimatantly saving each version of a components. There were times were I would make changes and not save a new version and need the old version I had just erased.
- Document problems faced as they are faced so that when you need to write about it for the presentation or somehting else you already have it written down so you can remember more details.

What words of wisdom would you pass on to future students?

- Make more clear expectations and communicate them clearly to keep meetings and communication as easy as possible.
- Document everything. You will thank yourself later.
- Keep all group files organized as you go. This will make it easier to find things and save time later.

What new knowledge or skills did you acquire throughout capstone.

- I definitely further progressed my skill and knowledge in 3D modeling and CAD software in general. If I use something similar in the future it will be alot easier to pick up.
- Team and project leadership
- How to create and present a good technical presentation
- Project intergration. Seeing and understanding how everyone's subsystems worked together to create our robot.

What classes have you taken that helped you in capstone? What did they help with?

- ECE 4370 : Mechatronics showed me intergration with full systems from the ground up really well. I felt like it prepared me to be able to understand everyone else's subsystems to be able to create a base that would be able to support all functionalities. This class also taught me great trouble shooting techniques that I was able to apply when helping teammates during the construction and experimentation.
- ECE 3920 : Professionalism prepared me for more of the organizational side of the project. I was able to apply the ethical decision making learned as well as how to give a technical presentation.
- ECE 2010,3060, 3160: EE Lab 1 & 2 and Digital Systems lab taught me the importance of and how to have great wiring techniques and convention, especially as it related to trouble shooting cirucits.
- To clarify, I created the chassis and all 3D printed components for the group. Therefore, a majority of my work was done with CAD softwares annd there is no CAD class as part of our curriculum.

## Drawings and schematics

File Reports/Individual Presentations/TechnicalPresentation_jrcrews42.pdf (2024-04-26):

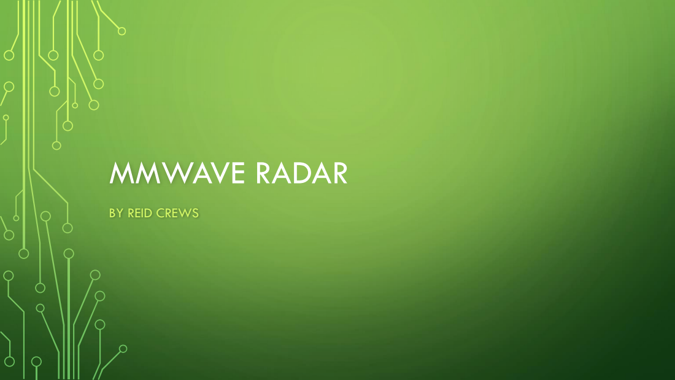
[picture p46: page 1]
MMWAVE RADAR

BY REID CREWS

# OVERVIEW

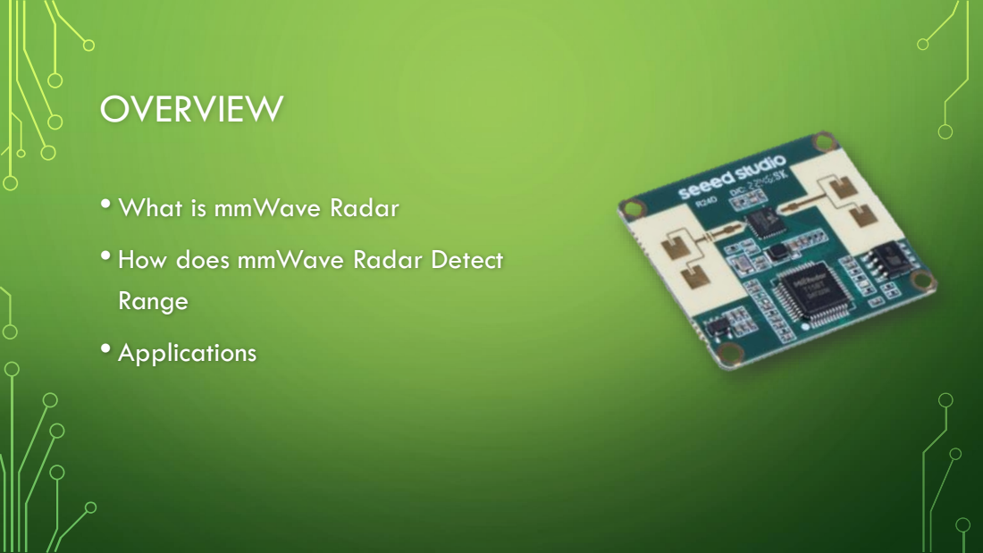
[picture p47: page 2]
Range; • Applications

• What is mmWave Radar

• How does mmWave Radar Detect

# WHAT IS MMWAVE RADAR

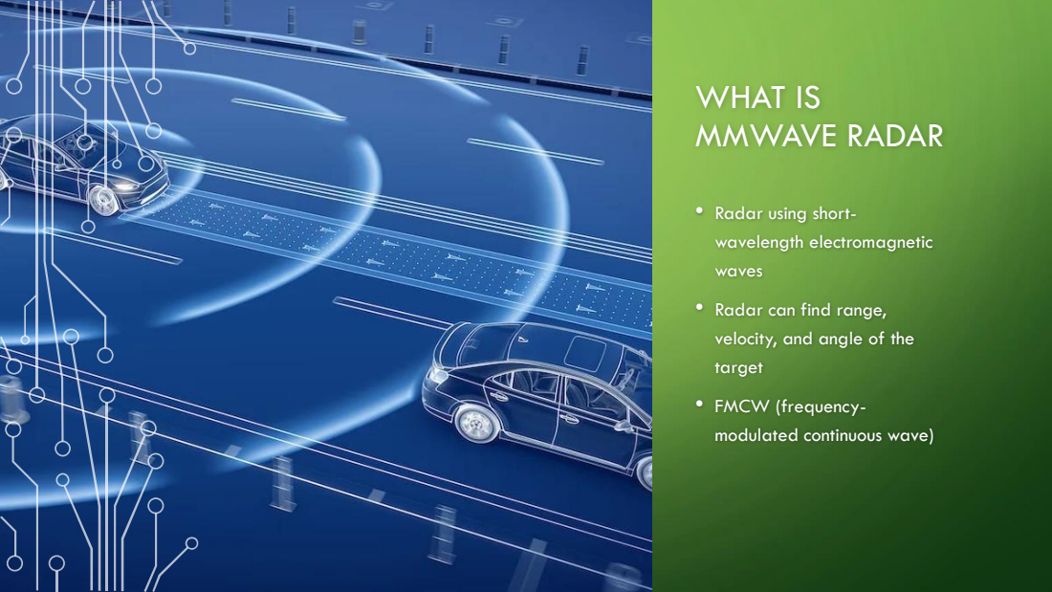
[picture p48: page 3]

• Radar using short-
wavelength electromagnetic
waves

• Radar can find range,
velocity, and angle of the
target

• FMCW (frequency-
modulated continuous wave)

# HOW DO THEY WORK

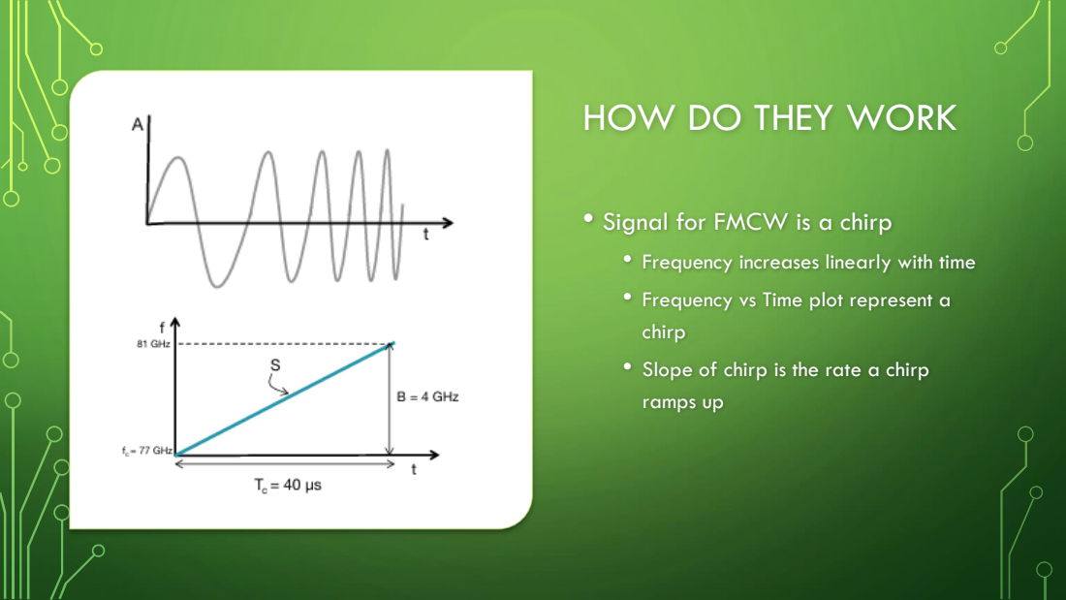
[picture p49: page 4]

• Signal for FMCW is a chirp

• Frequency increases linearly with time

• Frequency vs Time plot represent a
chirp
• Slope of chirp is the rate a chirp
ramps up

# GENERATE SIGNAL

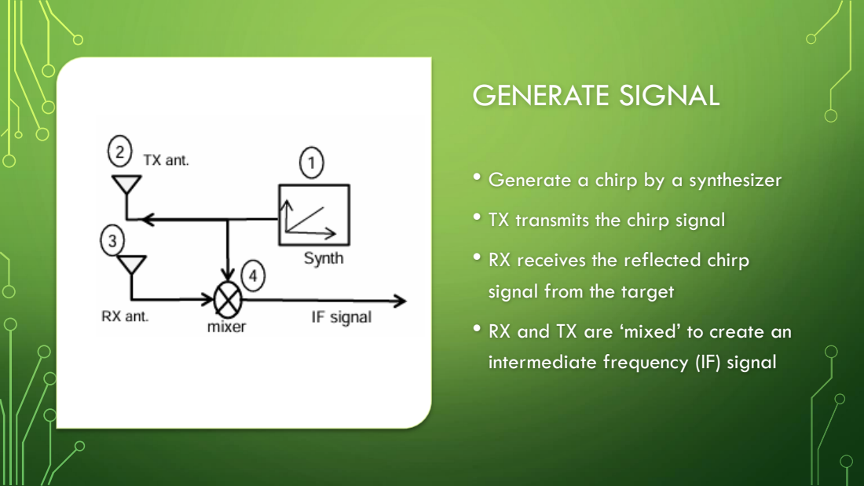
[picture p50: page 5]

• Generate a chirp by a synthesizer

• TX transmits the chirp signal

• RX receives the reflected chirp
signal from the target
• RX and TX are ‘mixed’ to create an
intermediate frequency (IF) signal

# MIXER

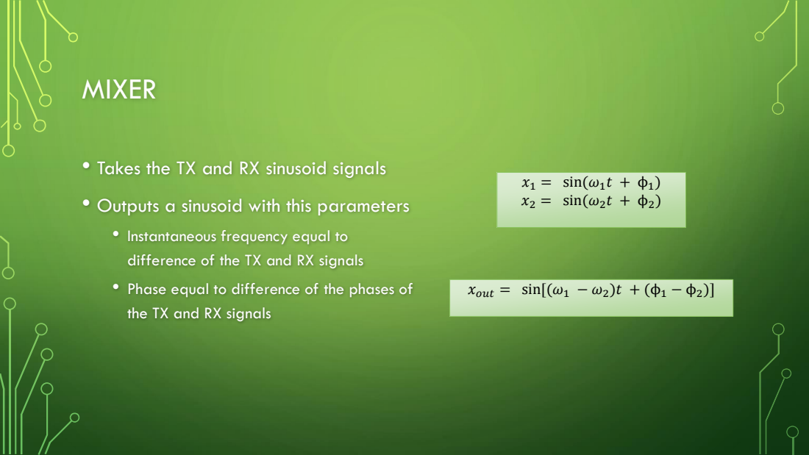
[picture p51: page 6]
x1 = sin(ω1t + ϕ1) x2 = sin(ω2t + ϕ2); xout = sin[(ω1 − ω2)t + (ϕ1 − ϕ2)]

• Takes the TX and RX sinusoid signals

• Outputs a sinusoid with this parameters

• Instantaneous frequency equal to
difference of the TX and RX signals
• Phase equal to difference of the phases of
the TX and RX signals

# IF SIGNAL

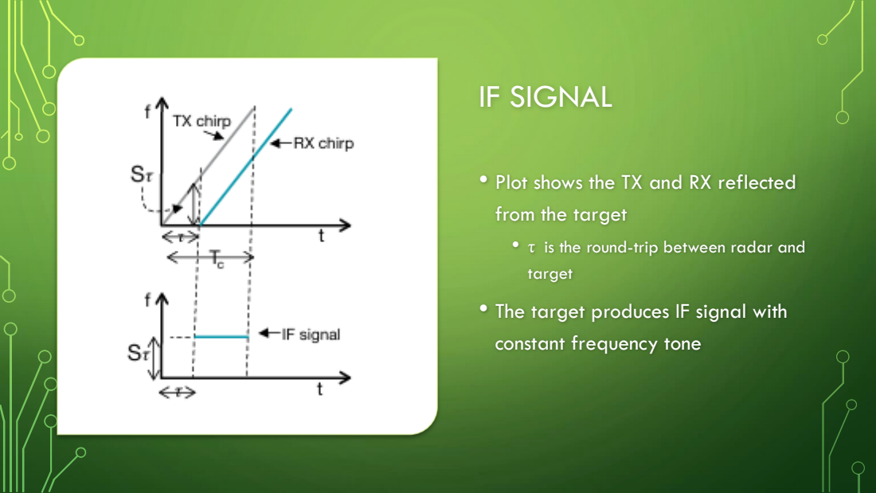
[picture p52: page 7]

• Plot shows the TX and RX reflected
from the target

• τ is the round-trip between radar and
target
• The target produces IF signal with
constant frequency tone

# EQUATION

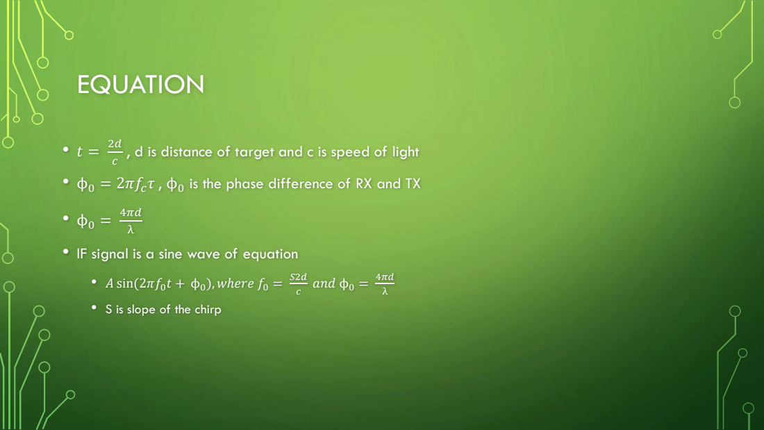
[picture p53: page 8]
• A sin(2πf0t + ϕ0), wℎere f0 =; and ϕ0 =

, d is distance of target and c is speed of light

• ϕ0 = 2πfcτ , ϕ0 is the phase difference of RX and TX

• IF signal is a sine wave of equation

• S is slope of the chirp

# APPLICATION

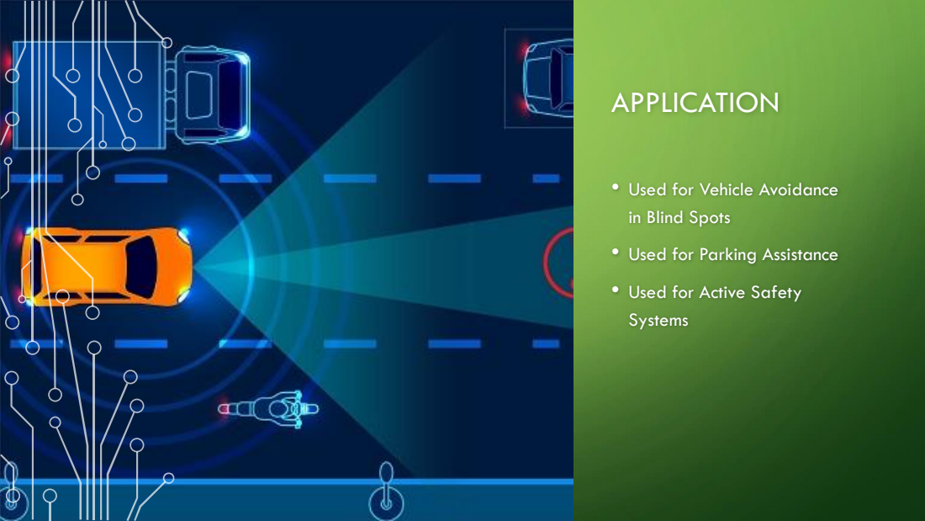
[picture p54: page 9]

• Used for Vehicle Avoidance
in Blind Spots

• Used for Parking Assistance

• Used for Active Safety
Systems

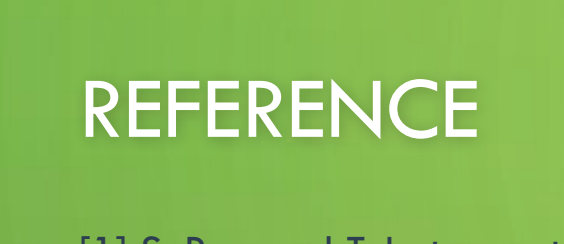
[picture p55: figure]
REFERENCE

[1] S. Rao and T. Instruments, “Introduction to mmwave Sensing: FMCW Radars.” Available: https://www.ti.com/content/dam/videos/externalvideos/2/3816841626001/5415528961001.mp4/subassets/mmwaveSensing-FMCWofflineviewing_0.pdf (https://www.ti.com/content/dam/videos/external-videos/2/3816841626001/5415528961001.mp4/subassets/mmwaveSensing-FMCW-offlineviewing_0.pdf)
[2] C. Radar, A. Manager, and S. Rao, “The fundamentals of millimeter wave radar sensors The fundamentals of millimeter wave radar sensors 2,” 2020. Available: https://www.ti.com/lit/wp/spyy005a/spyy005a.pdf?ts=1714029544115
[3] “mmWave Radar,” MediaTek. https://www.mediatek.com.es/products/mmwave-radar-2

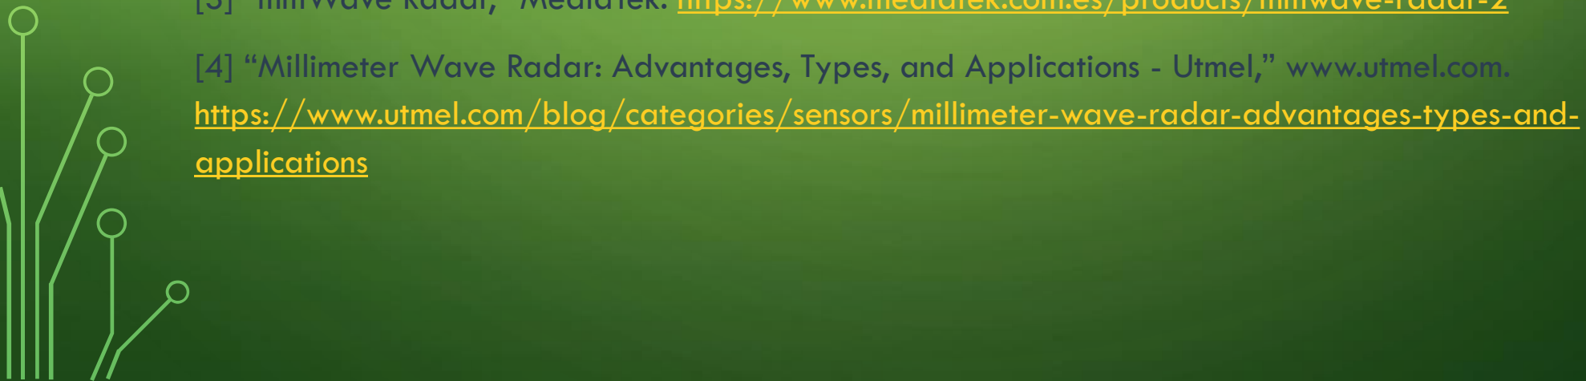
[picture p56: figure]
https://www.utmel.com/blog/categories/sensors/millimeter-wave-radar-advantages-types-and-; applications

[4] “Millimeter Wave Radar: Advantages, Types, and Applications - Utmel,” www.utmel.com.

[2]
[2]

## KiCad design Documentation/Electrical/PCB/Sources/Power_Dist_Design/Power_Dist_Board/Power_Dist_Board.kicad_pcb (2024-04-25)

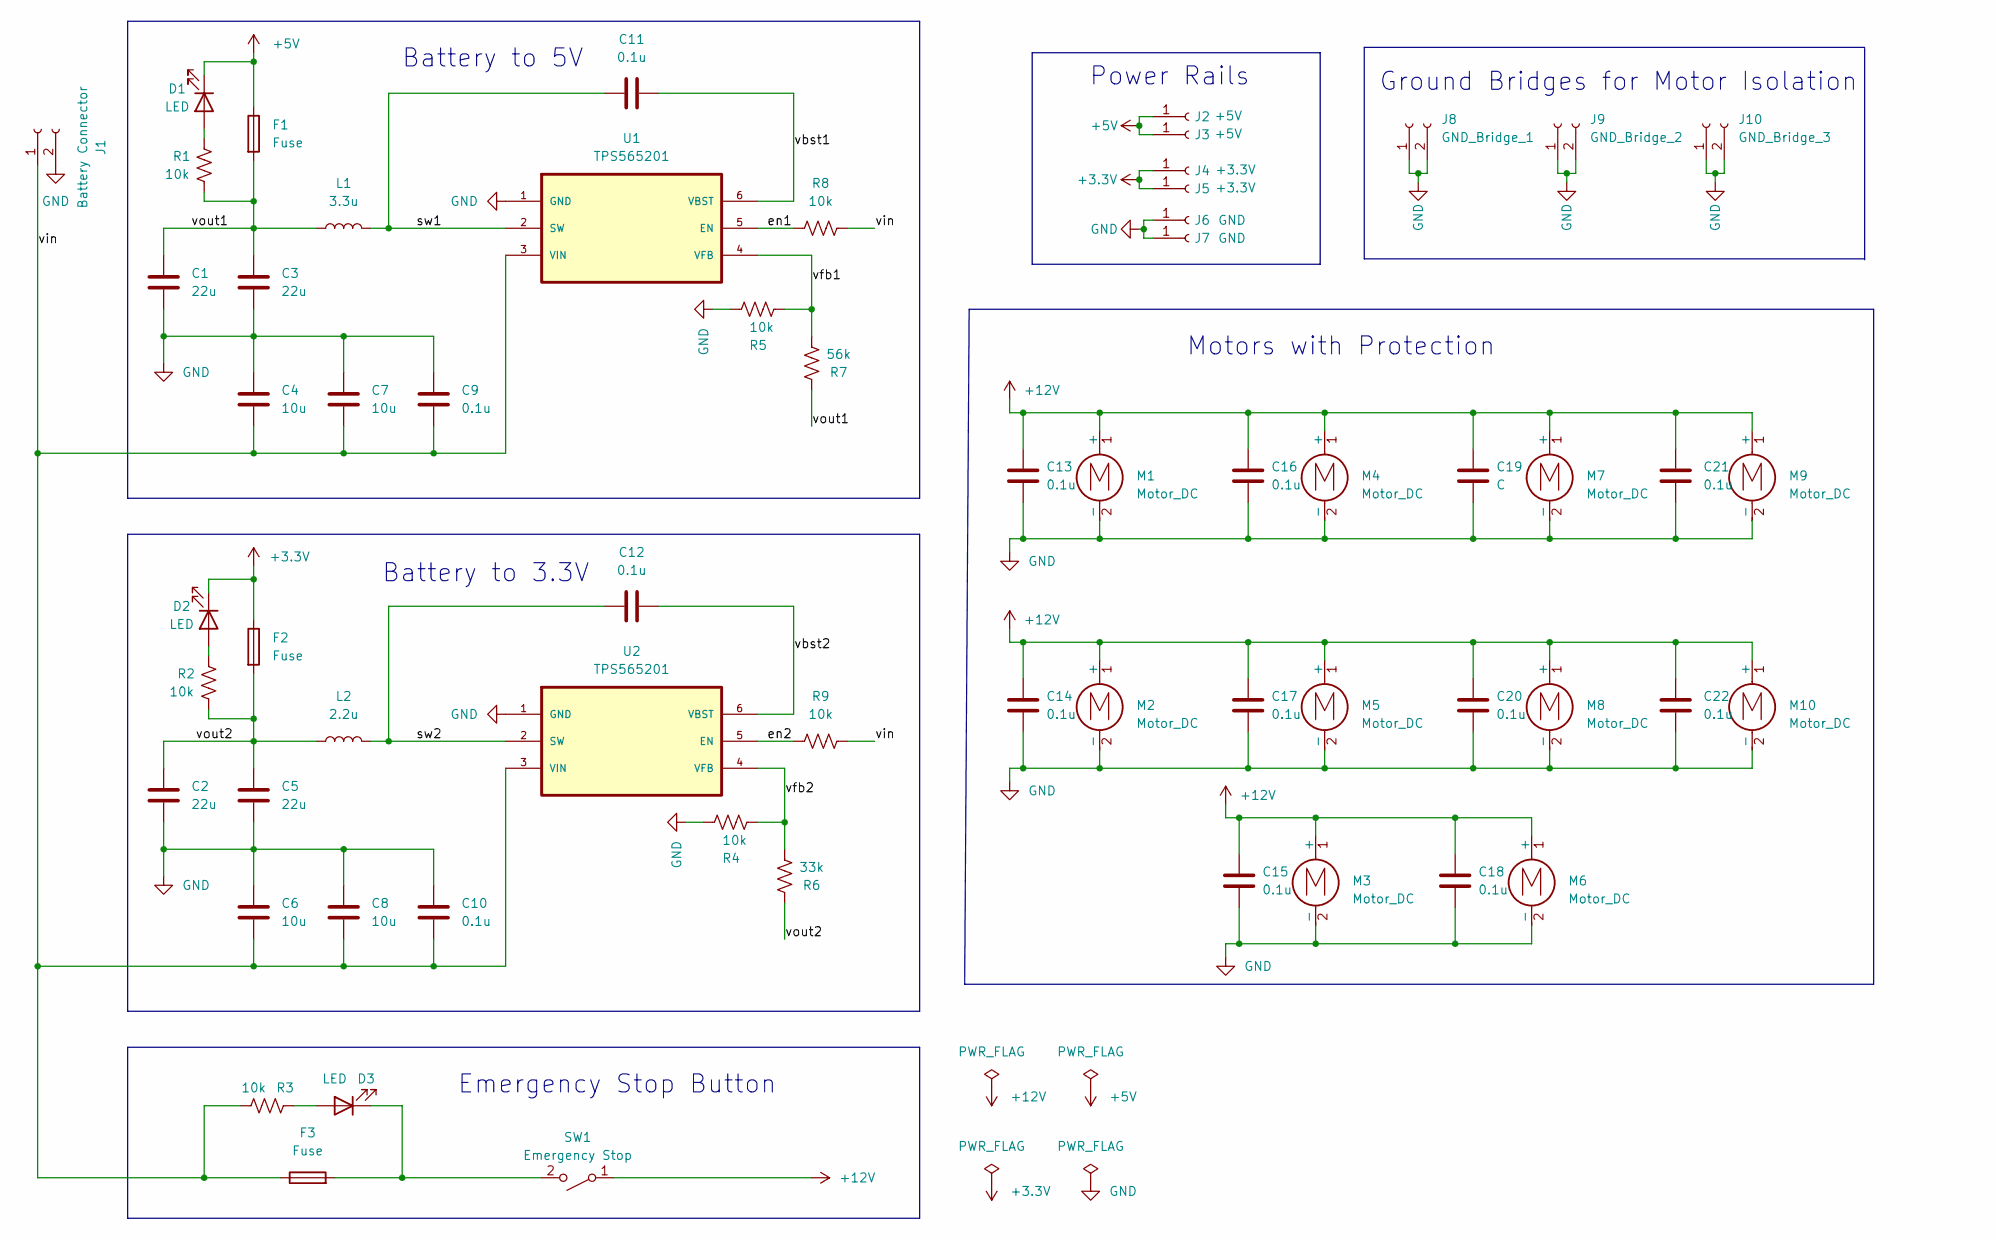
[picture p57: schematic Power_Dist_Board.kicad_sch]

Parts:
C1, C2, C3, C5: 22u; C_1206_3216Metric_Pad1.33x1.80mm_HandSolder
C4, C6, C7, C8: 10u; C_1206_3216Metric_Pad1.33x1.80mm_HandSolder
C9, C10, C11, C12, C13, C14, C15, C16, C17, C18, C20, C21, C22: 0.1u; C_1206_3216Metric_Pad1.33x1.80mm_HandSolder
C19: C; C_1206_3216Metric_Pad1.33x1.80mm_HandSolder
D1, D2, D3: LED; LED_1206_3216Metric_Pad1.42x1.75mm_HandSolder
F1, F2, F3: Fuse; Fuse_1206_3216Metric_Pad1.42x1.75mm_HandSolder
J1: Battery Connector; Molex_Screw_Term_0397730002
J2, J3: +5V; Pwr_Rail_Conn_Custom
J4, J5: +3.3V; Pwr_Rail_Conn_Custom
J6, J7: GND; Pwr_Rail_Conn_Custom
J8: GND_Bridge_1; GND_Bridge
J9: GND_Bridge_2; GND_Bridge
J10: GND_Bridge_3; GND_Bridge
L1: 3.3u; IND_SPM6530_TDK
L2: 2.2u; IND_SPM6530_TDK
M1, M2, M3, M4, M5, M6, M7, M8, M9, M10: Motor_DC; Molex_Screw_Term_0397730002
R1, R2, R3, R4, R5, R8, R9: 10k; R_1206_3216Metric_Pad1.30x1.75mm_HandSolder
R6: 33k; R_1206_3216Metric_Pad1.30x1.75mm_HandSolder
R7: 56k; R_1206_3216Metric_Pad1.30x1.75mm_HandSolder
SW1: Emergency Stop; Molex_Screw_Term_0397730002
U1, U2: TPS565201

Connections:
+3.3V: D2.1 (K), F2.1, J4.1, J5.1
+5V: D1.1 (K), F1.1, J2.1, J3.1
+12V: C13.1, C14.1, C15.1, C16.1, C17.1, C18.1, C19.1, C20.1, C21.1, C22.1, M1.1 (+), M2.1 (+), M3.1 (+), M4.1 (+), M5.1 (+), M6.1 (+), M7.1 (+), M8.1 (+), M9.1 (+), M10.1 (+), SW1.1 (A)
/en1: R8.1, U1.5 (EN)
/en2: R9.1, U2.5 (EN)
/sw1: C11.1, L1.2, U1.2 (SW)
/sw2: C12.1, L2.2, U2.2 (SW)
/vbst1: C11.2, U1.6 (VBST)
/vbst2: C12.2, U2.6 (VBST)
/vfb1: R5.2, R7.1, U1.4 (VFB)
/vfb2: R4.2, R6.1, U2.4 (VFB)
/vin: C4.2, C6.2, C7.2, C8.2, C9.2, C10.2, F3.1, J1.1, R3.1, R8.2, R9.2, U1.3 (VIN), U2.3 (VIN)
/vout1: C1.1, C3.1, F1.2, L1.1, R1.1, R7.2
/vout2: C2.1, C5.1, F2.2, L2.1, R2.1, R6.2
GND: C1.2, C2.2, C3.2, C4.1, C5.2, C6.1, C7.1, C8.1, C9.1, C10.1, C13.2, C14.2, C15.2, C16.2, C17.2, C18.2, C19.2, C20.2, C21.2, C22.2, J1.2, J6.1, J7.1, J8.1, J8.2, J9.1, J9.2, J10.1, J10.2, M1.2 (-), M2.2 (-), M3.2 (-), M4.2 (-), M5.2 (-), M6.2 (-), M7.2 (-), M8.2 (-), M9.2 (-), M10.2 (-), R4.1, R5.1, U1.1 (GND), U2.1 (GND)
unnamed: D1.2 (A), R1.2
unnamed: D2.2 (A), R2.2
unnamed: D3.2 (A), R3.2
unnamed: D3.1 (K), F3.2, SW1.2 (B)

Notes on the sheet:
Motors with Protection
Battery to 5V
Emergency Stop Button
Battery to 3.3V
Power Rails
Ground Bridges for Motor Isolation

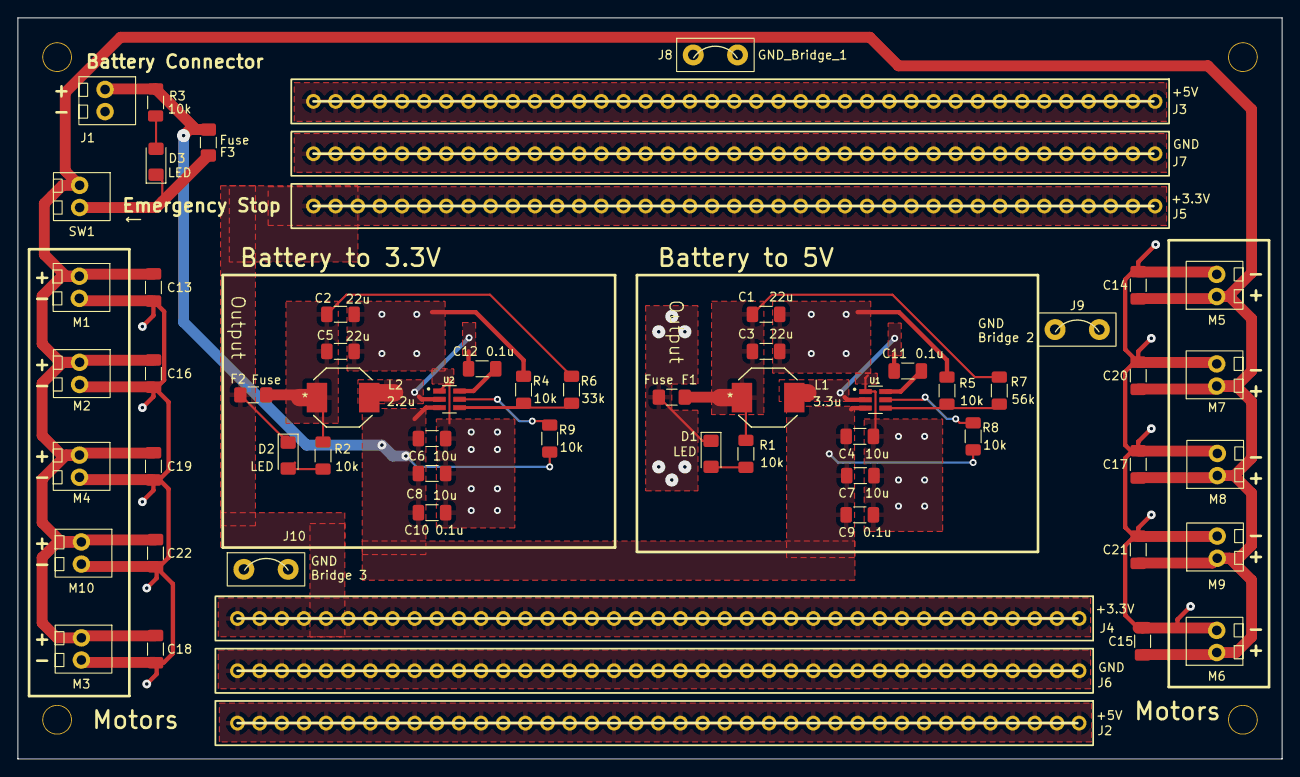
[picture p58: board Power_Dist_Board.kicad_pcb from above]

Board: 2 copper layers, 145.0 x 85.0 mm, 62 parts (0 on the bottom side), 19 nets.

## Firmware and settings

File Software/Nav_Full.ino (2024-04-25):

#include <Adafruit_Sensor_Calibration.h>
#include <Adafruit_AHRS.h>
#include <QTRSensors.h>
#include <Adafruit_VL53L0X.h>
#include <Ultrasonic.h>
#include <GyverOLED.h>
GyverOLED<SSH1106_128x64> oled;

/*
* Create accelerometer, gyroscope, magnetometer sensor values
*/
Adafruit_Sensor *accelerometer, *gyroscope, *magnetometer;

// uncomment one combo 9-DoF!
#include "LSM6DS_LIS3MDL.h"  // can adjust to LSM6DS33, LSM6DS3U, LSM6DSOX...

//Filter to convert orientation sensor data to heading, roll, pitch, etc.
Adafruit_Mahony filter;  // fastest/smalleset

#if defined(ADAFRUIT_SENSOR_CALIBRATION_USE_EEPROM)
  Adafruit_Sensor_Calibration_EEPROM cal;
#else
  Adafruit_Sensor_Calibration_SDFat cal;
#endif

#define FILTER_UPDATE_RATE_HZ 100
#define PRINT_EVERY_N_UPDATES 10


const uint8_t techLogo [] PROGMEM = {
0x00, 0x00, 0x00, 0x00, 0x00, 0x00, 0x00, 0x00, 0x00, 0x00, 0x00, 0x00, 0x00, 0x00, 0x00, 0x00,
0x00, 0x00, 0x00, 0x00, 0x00, 0x00, 0x00, 0x00, 0x00, 0x00, 0x00, 0x00, 0x00, 0x00, 0x00, 0x00,
0x00, 0x00, 0x00, 0x00, 0x00, 0x00, 0x00, 0x00, 0x00, 0x00, 0x00, 0x00, 0x00, 0x00, 0x00, 0x00,
0x00, 0x00, 0x00, 0x00, 0x00, 0x00, 0x00, 0x00, 0x00, 0x00, 0x00, 0x00, 0x00, 0x00, 0x00, 0x00,
0x00, 0x00, 0x00, 0x00, 0x00, 0x00, 0x00, 0x00, 0x00, 0x00, 0x00, 0x00, 0x00, 0x00, 0x00, 0x00,
0x00, 0x00, 0x00, 0x00, 0x00, 0x00, 0x00, 0x00, 0x00, 0x00, 0x00, 0x00, 0x00, 0x00, 0x00, 0x00,
0x00, 0x00, 0x00, 0x00, 0x00, 0x00, 0x00, 0x00, 0x00, 0x00, 0x00, 0x00, 0x00, 0x00, 0x00, 0x00,
0x00, 0x00, 0x00, 0x00, 0x00, 0x00, 0x00, 0x00, 0x00, 0x00, 0x00, 0x00, 0x00, 0x00, 0x00, 0x00,
0x00, 0x00, 0x00, 0x00, 0x00, 0x00, 0x00, 0x00, 0x00, 0x00, 0x00, 0x00, 0x00, 0x00, 0x00, 0x00,
0x00, 0x00, 0x00, 0x00, 0x00, 0x00, 0x00, 0x00, 0x00, 0x00, 0x00, 0x00, 0x00, 0x00, 0x00, 0x00,
0x00, 0x00, 0x00, 0x00, 0x00, 0x00, 0x00, 0x00, 0x00, 0x00, 0x00, 0x00, 0x00, 0x00, 0x00, 0x00,
0x00, 0x00, 0x00, 0x00, 0x00, 0x00, 0x00, 0x00, 0x00, 0x00, 0x00, 0x00, 0x00, 0x00, 0x00, 0x00,
0x00, 0x00, 0x00, 0x00, 0x00, 0x00, 0x00, 0x00, 0x00, 0x00, 0x00, 0x00, 0x00, 0x00, 0x00, 0x00,
0x00, 0x00, 0x00, 0x00, 0x00, 0x00, 0x00, 0x00, 0x00, 0x00, 0x00, 0x00, 0x00, 0x00, 0x00, 0x00,
0x00, 0x00, 0x00, 0x00, 0x00, 0x00, 0x00, 0x00, 0x00, 0x00, 0x00, 0x00, 0x00, 0x00, 0x00, 0x00,
0x00, 0x00, 0x00, 0x00, 0x00, 0x00, 0x00, 0x00, 0x00, 0x00, 0x00, 0x00, 0x00, 0x00, 0x00, 0x00,
0x00, 0x00, 0x00, 0x00, 0x00, 0x00, 0x00, 0x00, 0x00, 0x00, 0x00, 0x00, 0x00, 0x00, 0x00, 0x00,
0x00, 0x00, 0x00, 0x00, 0x00, 0x00, 0x00, 0x00, 0x00, 0x00, 0x00, 0x00, 0x00, 0x00, 0x00, 0x00,
0x00, 0x00, 0x00, 0x00, 0x00, 0x00, 0x00, 0x00, 0x00, 0x00, 0x00, 0x00, 0x00, 0x00, 0x00, 0x00,
0x00, 0x00, 0x00, 0xFC, 0xFC, 0xFC, 0xFC, 0x7C, 0x3C, 0x7C, 0xFC, 0x3C, 0x1C, 0xFC, 0xFC, 0xFC,
0xFC, 0xFC, 0xFC, 0xFC, 0xFC, 0x1C, 0x3C, 0xFC, 0x7C, 0x3C, 0x7C, 0xFC, 0xFC, 0xFC, 0xFC, 0x00,
0x00, 0x00, 0x00, 0x00, 0x00, 0x00, 0x00, 0x00, 0x00, 0x00, 0x00, 0x00, 0x00, 0x00, 0x00, 0x00,
0x00, 0x00, 0x00, 0x00, 0x00, 0x00, 0x00, 0x00, 0x00, 0x00, 0x00, 0x00, 0x00, 0x00, 0x00, 0x00,
0x00, 0x00, 0x00, 0x00, 0x00, 0x00, 0x00, 0x00, 0x00, 0x00, 0x00, 0x00, 0x00, 0x00, 0x00, 0x00,
0x00, 0x00, 0x00, 0x00, 0x00, 0x00, 0x00, 0x00, 0x00, 0x00, 0x00, 0x00, 0x00, 0x00, 0x00, 0x00,
0x00, 0x00, 0x00, 0x00, 0x00, 0x00, 0x00, 0x00, 0x00, 0x00, 0x00, 0x00, 0x00, 0x00, 0x00, 0x00,
0x00, 0x00, 0x00, 0x00, 0x00, 0x00, 0x00, 0x00, 0x00, 0x00, 0x00, 0x00, 0x00, 0x00, 0x00, 0x00,
0x00, 0x00, 0x00, 0x1F, 0x1F, 0x1F, 0x07, 0x00, 0x00, 0x00, 0x01, 0x00, 0x00, 0xFF, 0xFF, 0xFF,
0x7F, 0x7F, 0xFF, 0xFF, 0xFF, 0x00, 0x00, 0x01, 0x00, 0x00, 0x00, 0x07, 0x1F, 0x1F, 0x1F, 0x00,
0x00, 0x00, 0x00, 0x00, 0x00, 0x00, 0x00, 0x00, 0x00, 0x00, 0x00, 0x00, 0x00, 0x00, 0x00, 0x00,
0x00, 0x00, 0x00, 0x00, 0x00, 0x00, 0x00, 0x00, 0x00, 0x00, 0x00, 0x00, 0x00, 0x00, 0x00, 0x00,
0x00, 0x00, 0x00, 0x00, 0x00, 0x00, 0x00, 0x00, 0x00, 0x00, 0x00, 0x00, 0x00, 0x00, 0x00, 0x00,
0x00, 0x00, 0x00, 0x00, 0x00, 0x00, 0x00, 0x00, 0x00, 0x00, 0x00, 0x00, 0x00, 0x00, 0x00, 0x00,
0x00, 0x00, 0x00, 0x00, 0x00, 0x00, 0x00, 0x00, 0x00, 0x00, 0x00, 0x00, 0x00, 0x00, 0x00, 0x00,
0x00, 0x00, 0x00, 0x00, 0x00, 0x00, 0x00, 0x00, 0x00, 0x00, 0x00, 0x00, 0x00, 0x00, 0x00, 0x00,
0x00, 0x00, 0x00, 0x00, 0x00, 0x00, 0x07, 0x38, 0xC0, 0x00, 0x00, 0x00, 0x00, 0x0F, 0x01, 0x00,
0x00, 0x00, 0x04, 0x0E, 0x07, 0x00, 0x00, 0x00, 0x00, 0xC0, 0x38, 0x07, 0x00, 0x00, 0x00, 0x00,
0x00, 0x00, 0x00, 0x00, 0x00, 0x00, 0x00, 0x00, 0x00, 0x00, 0x00, 0x00, 0x00, 0x00, 0x00, 0x00,
0x00, 0x00, 0x00, 0x00, 0x00, 0x00, 0x00, 0x00, 0x00, 0x00, 0x00, 0x00, 0x00, 0x00, 0x00, 0x00,
0x00, 0x00, 0x00, 0x00, 0x00, 0x00, 0x00, 0x00, 0x00, 0x00, 0x00, 0x00, 0x00, 0x00, 0x00, 0x00,
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
};

uint32_t timestamp;
uint32_t u32_currentMillis = 0;
uint32_t u32_positionMillis = 0;
uint32_t u32_orientationMillis = 0;
uint32_t u32_locationMillis = 0;
uint32_t u32_objectDetectionMillis = 0;

QTRSensors qtr;
Adafruit_VL53L0X sensor1; //CHANGE
Adafruit_VL53L0X sensor2; //CHANGE
Adafruit_VL53L0X sensor3; //CHANGE
Adafruit_VL53L0X sensor4; //CHANGE
Adafruit_VL53L0X sensor5; //CHANGE
Adafruit_VL53L0X sensor6; //CHANGE
Adafruit_VL53L0X sensor7; //CHANGE
Adafruit_VL53L0X sensor8; //CHANGE

uint32_t u32_LineFollowingTime = 0;

const uint8_t SensorCount = 6;
uint16_t sensorValues[SensorCount];
sensors_event_t accel, gyro, mag;
String start = "<";
String end = ">";
String c = ",";

typedef struct {
  Adafruit_VL53L0X *psensor; // pointer to object
  TwoWire *pwire;
  int id;            // IIC id number for the sensor
  int shutdown_pin;  // which pin for shutdown;
  int interrupt_pin; // which pin to use for interrupts.
  Adafruit_VL53L0X::VL53L0X_Sense_config_t sensor_config; // options for how to use the sensor
  uint16_t range;        // range value used in continuous mode stuff.
  uint8_t sensor_status; // status from last ranging in continuous.
} sensorList_t;


// Setup for 8 sensors by defining information for each sensor in a 'sensors' array. Include
// a separate line of information for each sensor
sensorList_t sensors[] = {
  // For 'sensor1', define the IIC accress as hexadecimal value 0x30. Assign digital pin #38 to this 
  // sensor's XSHUT pin (shut-down pin). Assign digital pin #5 to the sensor's INTERRUPT pin.
  {&sensor1, &Wire, 0x30, 38, 5, Adafruit_VL53L0X::VL53L0X_SENSE_DEFAULT, 0, 0},

  // For 'sensor2', define the IIC accress as hexadecimal value 0x31. Assign digital pin #6 to this 
  // sensor's XSHUT pin (shut-down pin). Assign digital pin #7 to the sensor's INTERRUPT pin.
  {&sensor2, &Wire, 0x31, 6, 7, Adafruit_VL53L0X::VL53L0X_SENSE_DEFAULT, 0, 0},

  
  // For 'sensor3', define the IIC accress as hexadecimal value 0x32. Assign digital pin #40 to this 
  // sensor's XSHUT pin (shut-down pin). Assign digital pin #3 to the sensor's INTERRUPT pin.
  {&sensor3, &Wire, 0x32, 40, 3, Adafruit_VL53L0X::VL53L0X_SENSE_DEFAULT, 0, 0},
  
  // For 'sensor4', define the IIC accress as hexadecimal value 0x33. Assign digital pin #29 to this 
  // sensor's XSHUT pin (shut-down pin). Assign digital pin #30 to the sensor's INTERRUPT pin.
  {&sensor4, &Wire, 0x33, 29, 30, Adafruit_VL53L0X::VL53L0X_SENSE_DEFAULT, 0, 0},

  // For 'sensor5', define the IIC accress as hexadecimal value 0x34. Assign digital pin #31 to this 
  // sensor's XSHUT pin (shut-down pin). Assign digital pin #32 to the sensor's INTERRUPT pin.
  {&sensor5, &Wire, 0x34, 31, 32, Adafruit_VL53L0X::VL53L0X_SENSE_DEFAULT, 0, 0},

  // For 'sensor6', define the IIC accress as hexadecimal value 0x35. Assign digital pin #33 to this 
  // sensor's XSHUT pin (shut-down pin). Assign digital pin #34 to the sensor's INTERRUPT pin.
  {&sensor6, &Wire, 0x35, 33, 34, Adafruit_VL53L0X::VL53L0X_SENSE_DEFAULT, 0, 0},

  // For 'sensor7', define the IIC accress as hexadecimal value 0x36. Assign digital pin #35 to this 
  // sensor's XSHUT pin (shut-down pin). Assign digital pin #36 to the sensor's INTERRUPT pin.
  {&sensor7, &Wire, 0x36, 35, 36, Adafruit_VL53L0X::VL53L0X_SENSE_DEFAULT, 0, 0},
  
  // For 'sensor8', define the IIC accress as hexadecimal value 0x37. Assign digital pin #37 to this 
  // sensor's XSHUT pin (shut-down pin). Assign digital pin #38 to the sensor's INTERRUPT pin.
  {&sensor8, &Wire, 0x37, 37, 38, Adafruit_VL53L0X::VL53L0X_SENSE_DEFAULT, 0, 0}
  
};
const int COUNT_SENSORS = sizeof(sensors) / sizeof(sensors[0]); //CHANGE
uint16_t objectDetectRanges_mm[COUNT_SENSORS]; //CHANGE
struct Packet{
  uint16_t lineFollowing;
  uint32_t locationFront; //CHANGE
  uint32_t locationBack; //CHANGE
  uint32_t locationRight; //CHANGE
  uint32_t locationLeft; //CHANGE
  uint16_t objectDetectionSensors[8]; //CHANGE
  float heading;
  float roll;
  float pitch;
  float qw;
  float qx;
  float qy; 
  float qz;
};

Packet packet;
void run_Orientation();
void run_LineFollowing();
void run_Location();
void run_ObjectDetection();
void setup_ObjectDetection();
void initialize_ObjDetectSensors();

Ultrasonic ultrasonicFront(8); //CHANGE
Ultrasonic ultrasonicBack(9); //CHANGE
Ultrasonic ultrasonicRight(10); //CHANGE
Ultrasonic ultrasonicLeft(11); //CHANGE


void setup() {
  Serial.begin(115200);
  delay(200);
  oled.init();             
  oled.clear();
  setup_ObjectDetection();
  if (!cal.begin()) {
  } else if (! cal.loadCalibration()) {
  }
  if (!init_sensors()) {
  }

  setup_sensors();
  filter.begin(FILTER_UPDATE_RATE_HZ);
  timestamp = millis();
  
  Wire.begin();
  Wire.setClock(400000); // 400KHz

  cal.calibrate(mag);
  cal.calibrate(accel);
  cal.calibrate(gyro);

  qtr.setTypeRC();
  qtr.setSensorPins((const uint8_t[]){28, 27, 26, 25, 24, 23}, SensorCount);
  qtr.setEmitterPin(22);

  /*
  qtr_back.setTypeRC();
  qtr_back.setSensorPins((const uint8_t[]){48, 49, 50 , 51, 52, 53}, SensorCount);
  qtr_back.setEmitterPin(47);*/


  delay(500);
  pinMode(LED_BUILTIN, OUTPUT);
  digitalWrite(LED_BUILTIN, HIGH); // turn on Arduino's LED to indicate we are in calibration mode
  for (uint16_t i = 0; i < 400; i++)
  {
    qtr.calibrate();
  }
  digitalWrite(LED_BUILTIN, LOW); // turn off Arduino's LED to indicate we are through with calibration
  delay(2000);

}
uint32_t loopMillis =0;
void loop() {
  run_Orientation();
  run_LineFollowing();
  run_Location();
  run_ObjectDetection();
  if((millis() - loopMillis) > 3000){
    loopMillis = millis();
    oled.drawBitmap(0, 0, techLogo, 128, 64);
    oled.update();
  }
  Serial.println(start + packet.lineFollowing + c + packet.heading + c + packet.roll + c + packet.pitch + c + packet.qw + c + packet.qx + c + packet.qy + c + packet.qz + c + packet.locationFront + c + packet.locationRight + c + packet.locationBack + c + packet.locationLeft + c + packet.objectDetectionSensors[0] + c + packet.objectDetectionSensors[1] + c + packet.objectDetectionSensors[2] + c + packet.objectDetectionSensors[3] + c + packet.objectDetectionSensors[4] + c + packet.objectDetectionSensors[5] + c + packet.objectDetectionSensors[6] + c + packet.objectDetectionSensors[7]  + end);
}
void run_Orientation(){
  float roll, pitch, heading;
  float gx, gy, gz;
  
    timestamp = millis();
    // Read the motion sensors
    accelerometer->getEvent(&accel);
    gyroscope->getEvent(&gyro);
    magnetometer->getEvent(&mag);

    // Gyroscope needs to be converted from Rad/s to Degree/s
    // the rest are not unit-important
    gx = gyro.gyro.x * SENSORS_RADS_TO_DPS;
    gy = gyro.gyro.y * SENSORS_RADS_TO_DPS;
    gz = gyro.gyro.z * SENSORS_RADS_TO_DPS;

    // Update the SensorFusion filter
    filter.update(gx, gy, gz, 
                  accel.acceleration.x, accel.acceleration.y, accel.acceleration.z, 
                  mag.magnetic.x, mag.magnetic.y, mag.magnetic.z);

    // print the heading, pitch and roll
    roll = filter.getRoll();
    pitch = filter.getPitch();
    heading = filter.getYaw();
    packet.heading = heading;
    packet.pitch = pitch;
    packet.roll = roll;

    float qw, qx, qy, qz;
    filter.getQuaternion(&qw, &qx, &qy, &qz);
    packet.qw = qw;

    packet.qx = qx;

    packet.qy = qy;

    packet.qz = qz;
}
void run_LineFollowing(){
  u32_currentMillis = millis();
  if((u32_currentMillis - u32_LineFollowingTime)>=250){
    uint16_t position = qtr.readLineBlack(sensorValues);
    // print the sensor values as numbers from 0 to 1000, where 0 means maximum
    // reflectance and 1000 means minimum reflectance, followed by the line
    // position
    /*for (uint8_t i = 0; i < SensorCount; i++)
    {
      Serial.print(sensorValues[i]);
      Serial.print('\t');
    }*/
    packet.lineFollowing = position; 
  }
}
void run_Location(){
  u32_currentMillis = millis();
  if((u32_currentMillis - u32_positionMillis) > 60){
    u32_positionMillis = u32_currentMillis;
    packet.locationFront = ultrasonicFront.MeasureInMillimeters();
    packet.locationBack = ultrasonicBack.MeasureInMillimeters();
    packet.locationRight = ultrasonicRight.MeasureInMillimeters();
    packet.locationLeft = ultrasonicLeft.MeasureInMillimeters();
  }
}
void run_ObjectDetection(){
  // Read the data from the sensors using a 'for' loop:
  for (int i = 0; i < COUNT_SENSORS; i++) {
    objectDetectRanges_mm[i] = sensors[i].psensor->readRange();  // This is where the sensor's data is captured
    packet.objectDetectionSensors[i] = objectDetectRanges_mm[i];
  }
}

/*
*Function Name: initialize_ObjDetectSensors
*Parameters: None
*Returns: void
*Description: Initialize the Object Detection Sensors
*/

void initialize_ObjDetectSensors(){
  bool found_any_sensors = false;
  // Set all shutdown pins low to shutdown sensors
  for (int i = 0; i < COUNT_SENSORS; i++)
    digitalWrite(sensors[i].shutdown_pin, LOW);
  delay(10);

  for (int i = 0; i < COUNT_SENSORS; i++) {
    // one by one enable sensors and set their ID
    digitalWrite(sensors[i].shutdown_pin, HIGH);
    delay(10); // give time to wake up.
    if (sensors[i].psensor->begin(sensors[i].id, false, sensors[i].pwire,
                                  sensors[i].sensor_config)) {
      found_any_sensors = true;
    }
  }

}

/*
*Function Name: setup_ObjectDetection
*Parameters: None
*Returns: void
*Description: Setup the ObjDetect Sensors by Shutdown Pins 
*  then using initialize function
*/

void setup_ObjectDetection(){
  for (int i = 0; i < COUNT_SENSORS; i++) {
    pinMode(sensors[i].shutdown_pin, OUTPUT);
    digitalWrite(sensors[i].shutdown_pin, LOW);
  }
  initialize_ObjDetectSensors();

}

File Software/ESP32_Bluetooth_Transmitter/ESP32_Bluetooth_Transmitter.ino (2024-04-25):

/*
* Coding structure provided by: https://randomnerdtutorials.com/esp-now-esp32-arduino-ide/
* Modified by: Isaac Hoese
* Purpose: Transmitter code for ESP32 data transmission
*/

#include <esp_now.h>
#include <WiFi.h>

#define RXp2 16
#define TXp2 17

// REPLACE WITH YOUR ESP RECEIVER'S MAC ADDRESS
uint8_t broadcastAddress1[] = {0x40,0x91,0x51,0x2D,0x4D,0x4C};

char* tempParse;
typedef struct test_struct {
  uint16_t lineFollowing;
  float heading;
  float roll;
  float pitch;
  float Qw;
  float Qx;
  float Qy;
  float Qz;
  uint32_t US1;
  uint32_t US2;
  uint32_t US3;
  uint32_t US4;
  uint16_t TOF1;
  uint16_t TOF2;
  uint16_t TOF3;
  uint16_t TOF4;
  uint16_t TOF5;
  uint16_t TOF6;
  uint16_t TOF7; 
  uint16_t TOF8;
} test_struct;

test_struct test;
bool b_goRead = false;
char c_readTemp;
uint8_t u8_readIndex = 0;
const uint8_t u8_startMark = '<';
const uint8_t u8_endMark = '>';
bool b_isEnd = false;
const uint8_t u8_receivedSize = 100;
char au8_receivedData[u8_receivedSize];

esp_now_peer_info_t peerInfo;

// callback when data is sent
void OnDataSent(const uint8_t *mac_addr, esp_now_send_status_t status) {
  char macStr[18];
  Serial.print("Packet to: ");
  // Copies the sender mac address to a string
  snprintf(macStr, sizeof(macStr), "%02x:%02x:%02x:%02x:%02x:%02x",
           mac_addr[0], mac_addr[1], mac_addr[2], mac_addr[3], mac_addr[4], mac_addr[5]);
  Serial.print(macStr);
  Serial.print(" send status:\t");
  Serial.println(status == ESP_NOW_SEND_SUCCESS ? "Delivery Success" : "Delivery Fail");
}

void read_Serial(){
  Serial.print("Received from serial: ");
  while (Serial2.available() && b_isEnd == false) {
    c_readTemp = Serial2.read();
    Serial.print(c_readTemp);
    if (c_readTemp == u8_startMark) {  //Check for starting point
      b_goRead = true;
    } else if (b_goRead) {
      if (c_readTemp == u8_endMark) {  //Check for ending point and terminate the array with null
        au8_receivedData[u8_readIndex] = '\0';
        b_goRead = false;
        b_isEnd = true;
        u8_readIndex = 0;
      } else {
        au8_receivedData[u8_readIndex] = c_readTemp;
        u8_readIndex++;
      }// end if-else
    }// end if-else
  }// end while
  Serial.println("");
}

void parse(){
  char* tempParse;

  tempParse = strtok(au8_receivedData, ",");
  test.lineFollowing = atoi(tempParse);
  tempParse = strtok(NULL, ",");
  test.heading = atof(tempParse);
  tempParse = strtok(NULL, ",");
  test.roll = atof(tempParse);
  tempParse = strtok(NULL, ",");
  test.pitch = atof(tempParse);
  tempParse = strtok(NULL, ",");
  test.Qw = atof(tempParse);
  tempParse = strtok(NULL, ",");
  test.Qx = atof(tempParse);
  tempParse = strtok(NULL, ",");
  test.Qy = atof(tempParse);
  tempParse = strtok(NULL, ",");
  test.Qz = atof(tempParse);
  tempParse = strtok(NULL, ",");
  test.US1 = atoi(tempParse);
  tempParse = strtok(NULL, ",");
  test.US2 = atoi(tempParse);
  tempParse = strtok(NULL, ",");
  test.US3 = atoi(tempParse);
  tempParse = strtok(NULL, ",");
  test.US4 = atoi(tempParse);
  tempParse = strtok(NULL, ",");
  test.TOF1 = atoi(tempParse);
  tempParse = strtok(NULL, ",");
  test.TOF2 = atoi(tempParse);
  tempParse = strtok(NULL, ",");
  test.TOF3 = atoi(tempParse);
  tempParse = strtok(NULL, ",");
  test.TOF4 = atoi(tempParse);
  tempParse = strtok(NULL, ",");
  test.TOF5 = atoi(tempParse);
  tempParse = strtok(NULL, ",");
  test.TOF6 = atoi(tempParse);
  tempParse = strtok(NULL, ",");
  test.TOF7 = atoi(tempParse);
  tempParse = strtok(NULL, ",");
  test.TOF8 = atoi(tempParse);
}

void setup() {
  Serial.begin(9600);
  Serial2.begin(115200, SERIAL_8N1, RXp2, TXp2);

  WiFi.mode(WIFI_STA);
 
  if (esp_now_init() != ESP_OK) {
    Serial.println("Error initializing ESP-NOW");
    return;
  }
  
  esp_now_register_send_cb(OnDataSent);
   
  // register peer
  peerInfo.channel = 0;  
  peerInfo.encrypt = false;
  // register first peer  
  memcpy(peerInfo.peer_addr, broadcastAddress1, 6);
  if (esp_now_add_peer(&peerInfo) != ESP_OK){
    Serial.println("Failed to add peer");
    return;
  }
}
void loop() {
  read_Serial();
  if(b_isEnd){
    parse();
    b_isEnd = false;
  }

  esp_err_t result = esp_now_send(0, (uint8_t *) &test, sizeof(test_struct));
  delay(10);
}

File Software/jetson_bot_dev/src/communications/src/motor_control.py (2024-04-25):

#!/usr/bin/env python3

#Motor_control.py takes in a twist message and sends a serial stream to the motors
#Format: Signed binary with the sign bit being 0 for positive and 1 for negative.
#           Two Bytes will be sent as {Linear_Vel Angular_Vel} with the latter 7 bits signifiying magnitude.
#Author: Isaac Jennings ijennings42@robotictechtn.com FIXME

import serial
import time



linear_vel = 100
angular_vel = 0

ser = serial.Serial(
    '/dev/ttyACM0',
    115200,
    timeout=1.0, 
)
time.sleep(3.0) #Setup Time Wait
ser.reset_input_buffer()
print("Serial OK")

try:
    while True:
        time.sleep(1)
        print("Sent MSG")
        ser.write(bin(linear_vel) + bin(angular_vel))
        
except KeyboardInterrupt:
    print("Close Serial Comm")
    ser.close()

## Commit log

2023-10-27 Added Sensor 6 Photos
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2023-10-27 Create 6 Bracket Assembly.jpg
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2023-10-27 3D models and updates to attachment sign off
    [1-4 washer.ipt, 1-4-20 screw.ipt, 2 Backet Adjustment.ipt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]
2023-10-27 Create 2 Sensor Assembly.jpg
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2023-10-29 Create Time of Flight Sensor Front.png
2023-10-29 Create Motor Connection Drawing.jpg
2023-10-30 Create Line Sensor 2 Attachment Assembly Drawing.jpg
2023-10-31 Made further edits to pcb
    [Power_Dist_Board.kicad_pcb, Power_Dist_Board.kicad_sch]
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2023-10-31 Update AbigailKennedy-Signoff-MotorControl
    Added my content without pictures
2023-10-31 Rename AbigailKennedy-Signoff-MotorControl to AbigailKennedy-Signoff-MotorControl.md
    Made md file type
2023-10-31 Increased width of 12V rail traces
    [Power_Dist_Board.kicad_pcb]
2023-10-31 Update AbigailKennedy-Signoff-MotorControl.md
    Fixed formatting without images
2023-10-31 Added motor control images
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2023-10-31 Added more motor terminals
    [Power_Dist_Board.kicad_pcb, Power_Dist_Board.kicad_sch]
2023-11-03 Update Nav-Microcontroller-Signoff.md
    Added information under schematic
2023-11-04 Added Images for Nav-Microcontroller Signoff
    Added Arduino Pinout and Grove Connections
2023-11-06 Update Motor Attachment Drawing.jpg
2023-11-06 Updated the Location Schematic
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2023-11-06 Added to signoff
    [Battery_Management.kicad_pcb, Battery_Management.kicad_sch]
2023-11-07 Added to batt manage signoff
    [Battery_Management.kicad_sch]
2023-11-08 Update Chassis Frame Sign Off.md
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2023-11-09 Removed extra pcb file from power-dist-signoff branch to fix merging conflict
2023-11-10 Update Orientation-Signoff.md
    Added information on the gyroscope degrees
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2023-11-13 Update AbigailKennedy-Signoff-MotorControl.md
    edited for signoff about to add photo
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2023-11-14 Added Nav-Arduino Schematic
    [Arduino_Signoff.kicad_pcb, Arduino_Signoff.kicad_sch, Orientation_Signoff.kicad_pcb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]
2023-11-14 Added dimensions to pcb
    [Power_Dist_Board.kicad_pcb]
2023-11-14 Add reidcrews ObjDetect and Location sensors to Arduino Schematic
    [Arduino_Signoff.kicad_sch]
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2023-11-15 Slight pcb changes
    [Power_Dist_Board.kicad_sch]
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2023-11-15 Made final edits to pcb for ground isolation and EMI mitigation
    [Power_Dist_Board.kicad_pcb]
2023-11-15 Added a few sentences about the ground isolation added to the ground plane and updated pcb image
2023-11-15 Commiting in case of small changes
    [Power_Dist_Board.kicad_pcb, bom.csv, designators.csv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]
2023-11-15 Edited pcb to give better grounding layout
    [Power_Dist_Board.kicad_pcb, bom.csv, designators.csv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]
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2023-11-18 Changed ground plane and added jumpers to motor-ground and ground connection
    [Power_Dist_Board.kicad_pcb, Power_Dist_Board.kicad_sch]
2023-11-18 Removed accidental battery signoff document from main branch
2023-11-18 Finalized pcb
    [Power_Dist_Board.csv, Power_Dist_Board.kicad_pcb, Power_Dist_Board.kicad_sch]
2023-11-20 Removed conflicting pcb files
    [Battery_Management.kicad_pcb, Battery_Management.kicad_sch, Power_Dist_Board.kicad_pcb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]
2023-11-21 Added screw holes to board and generated gerber file
    [Power_Dist_Board.kicad_pcb, bom.csv, designators.csv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]
2023-11-24 Adding CAD Files
    [1-4 washer.ipt, 1-4-20 screw.ipt, 2 Backet Adjustment.ipt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]
2023-11-24 Reduced length by 5mm to fit in chassis
    [Power_Dist_Board-B_Cu.gbr, Power_Dist_Board-B_Mask.gbr, Power_Dist_Board-B_Paste.gbr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]
2023-11-28 Added to wireless charging signoff
    [Power_Dist_Board-B_Cu.gbr, Power_Dist_Board-B_Mask.gbr, Power_Dist_Board-B_Paste.gbr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]
2023-11-28 Removed redundant folder
    [Power_Dist_Board-B_Cu.gbr, Power_Dist_Board-B_Mask.gbr, Power_Dist_Board-B_Paste.gbr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]
2023-11-28 Removed extra csv file
    [positions.csv]
2023-11-29 Organizing the Github
    [1-4 washer.ipt, 1-4-20 screw.ipt, 2 Backet Adjustment.ipt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]
2023-12-12 Added keepout zones under inductors that were accidentally removed at some point
    [Power_Dist_Board-B_Cu.gbr, Power_Dist_Board-B_Mask.gbr, Power_Dist_Board-B_Paste.gbr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]
2024-01-22 Removed conflicting old versions of pcb files
    [Power_Dist_Board.csv, Power_Dist_Board.kicad_pcb, Power_Dist_Board.kicad_sch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]
2024-01-28 A few small changes to WPT charging signoff
2024-02-03 Added notes from testing the pcb, battery, and charger
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2024-03-18 Add files via upload
    Added an updated schematic for motor control to show the fix for pin 4 not working
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2024-03-24 added plug-minus to battery terminal
    [Power_Dist_Board.kicad_pcb, bom.csv, designators.csv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]
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2024-04-13 added battery data and plots
    [battery_data.csv]
2024-04-13 added battery life estimate
    [battery_data.csv]
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2024-04-13 added 3d models to pcb
    [397730002.stp, Power_Dist_Board.kicad_pcb, Power_Dist_Board.kicad_sch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]
2024-04-13 small changes to power pcb
    [Power_Dist_Board.kicad_pcb, Power_Dist_Board.kicad_sch]
2024-04-13 generated new gerber
    [bom.csv, designators.csv, positions.csv]
2024-04-13 all 3d models added to board
    [397730002.stp, Power_Dist_Board.kicad_pcb]
2024-04-13 generated gerber
    [Power_Dist_Board.kicad_pcb]
2024-04-14 tried to export 3d model to blender, didn't work. Also got image of pcb
    [Power_Dist_Board.kicad_pcb, Power_Dist_Board.step]
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2024-04-23 added poster and to lessons learned
    [INN_Topology.dwg]
2024-04-24 added schematic of power board as pdf
    [Power_Dist_Board.kicad_sch]
2024-04-25 3D models
    [6 Backet Adjustment 2.0.ipt, 6 Backet Adjustment 3.0 short.ipt, 6 Backet Adjustment 3.0.ipt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]
2024-04-25 Moved BOM
    [Final BOM.xlsx]
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
